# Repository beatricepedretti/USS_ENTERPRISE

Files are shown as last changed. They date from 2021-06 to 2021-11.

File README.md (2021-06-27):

# AY2021_II_Project_1-1

This repository contains the code and files for the Final Project 1 - Variant 1. Academic Year 2020/2021, II Semester

Our project consists in developing a system able to perform a three-dimensional scanning of an object using two servomotors (MG996R) and one ultrasonic sensor (HCSR04). Our sonar must be opportunely moved to detect the distance surfaces in the field of view of the USS.

<h2>Software requirements</h2>
In order to let our device perform the functionality previously described, some software requirements must be fulfilled. Since our codes are written in PSoC and python, the following IDEs and softwares must be downloaded:
<ul>
  <li>PSoC Creator</li>
  <li>Kivy</li>
  <li>Visual Studio Code</li>
  <li>MATLAB 2017b version with Computer Visio Toolbox</li>
  <li>Autodesk Fusion 360</li>
</ul>

<h2>Hardware requirements</h2>

In order to create our device different components have been used. 
<ul>
  <li>Two servomotors</li>
  <li>Connection elements in order to link the two servomotors and create a serial chain able to scan the proximal environment
  <li>An ultrasonic sensor, the HCSR04</li>
  <li>A cypress board</li>
  <li>An homemade wooden box that acts as a housing for the board and guarantees robustness and stability to the serial chain</li>
</ul>
All these components must be properly handled as follow.

<h3>Board settings</h3>

The board is placed inside the wooden box with custom sliding plexiglass cover, and it is powered by the computer. The connection between the board and the computer can be performed using any COM the user wants, it will be recognized by our code. 

<h3>Servomotors settings</h3>

The first servomotor must be connected to 2.6 PIN and it must have the crankshaft positioned vertically. The second servomotor must be connected at the 2.7 PIN and placed at the top of the first servomotor with the crankshaft positioned horizontally. Both of the servos need an external power supply in order to work properly.

<h3>Ultrasonic sensor settings</h3>

The HCSR04 must be linked to the crankshaft of the second servomotor through a special connection element in order to move solidly with this crankshaft. It works thanks to two connections, the Echo, the Trigger, that must be connected respectively to the 2.5 and 2.4 PINs. The cables are shielded with copper wires to prevent interference from the servo motor wiring and help reduce electronic noise.

<h3>Complete device arrangement</h3>

This repository contains the 'CAD' folder with the solidworks file of our configuration. It is possible to recreate the device following the image, as long as the user has all the components listed before. 

<h2>Calibration procedure and angle-coordinates conversion</h2>

It is possible to see and understand the conversion from angles to three-dimensional coordinates in the image below. In the following chapter the computation, that allows the representation of the object put in front of our device, will be described.

<h3>X-Y-Z system</h3>

The Z-axis is the extension of the crankshaft of the first servomotor and it remains integral with it. This servomotor is placed in the exact middle of the X-axis so that the bottom of its crankshaft consists in the origin of the reference system. Y-axis is aligned with the direction of the long side of the first servo motor. REMEMBER: the second servomotor rotates jointly and solidally with the crankshaft of the first servomotor.

<h3>Angles description</h3>

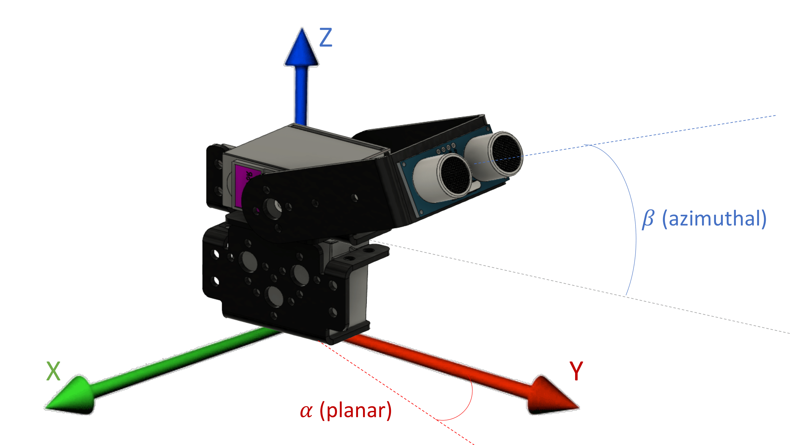
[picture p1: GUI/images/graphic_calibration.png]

 
The rotation of the crankshaft 1 allows to sweep the XY plane, its motion is described by the alpha angle. <i>Alpha is the angle between the Y-axis and the plane perpendicular to XY, containing the point detected and aligned with the direction of the arm to which the sonar is linked.</i><br>
The rotation of the crankshaft 2 allows to sweep the plane perpendicular to XY and aligned with the direction of the long side of the second servomotor and its motion is described by the beta angle. <i>Beta is the angle between the straight line determined by the arm to which the sonar is attached and the plane on which the crankshaft of the second servo motor lies.</i><br>
Functions getPosition() and setPosition(X°) allow to, respectively, return and set the angle (degrees) of one servo motor.  

First servomotor: 
<ul>
  <li>0 angle: lies on the positive portion of the X-axis</li>
  <li>90 angle: lies on the positive portion of the Y-axis</li>
  <li>180 angle: lies on the negative portion of the X-axis</li>
</ul>
In order to scan the width of the object put in front of the device, the first servomotor will sweep a 100° angle, starting from 40° up to 140°.

Second servomotor:
<ul>
  <li>0 angle: due to structural reason it consists in a 60° angle between the Z-axis and the straight line which is the extension of the arm to which the sonar is linked.</li>
  <li>90 angle: 0 angle + 90° = 150° (almost)</li>
</ul>
In order to scan the height of the object put in front of the device, the second servomotor will sweep a 60° angle, starting from 60° up to 120°.<br><br>
According to the information reported:<br>

SERVO_MID_ANGLE=90<br>
ANGLE_ZERO=60<br>
<i>alpha = SERVO_MID_ANGLE-Servo_GetPosition1()</i><br>
<i>beta = Servo_GetPosition2()+ANGLE_ZERO-SERVO_MID_ANGLE</i><br>

<h3>Coordinates computation</h3>

Knowing that :
<ul>
  <li>D2 is the distance between the middle of the crankshaft of the second servomotor and the Z-axis</li>
  <li>ARM_LENGTH is the length of the connection component that allows the rotation of the sonar solidally with the second crankshaft</li>
  <li>pos_servo1_rad is alpha in rad</li>
  <li>pos_servo2_rad is beta in rad</li>
  <li>pos_servo2_z_rad is beta+ANGLE_ZERO° in rad</li>
  <li>Z1 is the height of the crankshaft of the second servomotor</li>
</ul>
the coordinates computed using those two angles are:<br>

<i>X=(D2+(ARM_LENGTH+distance_real)*cos(pos_servo2_rad))*sin(pos_servo1_rad);</i><br>
<i>Y=(D2+(ARM_LENGTH+distance_real)*cos(pos_servo2_rad))*cos(pos_servo1_rad);</i><br>
<i>Z=Z1-(ARM_LENGTH+distance_real)*cos(pos_servo2_z_rad);</i><br>

<h2>Configuration through GUI</h2>
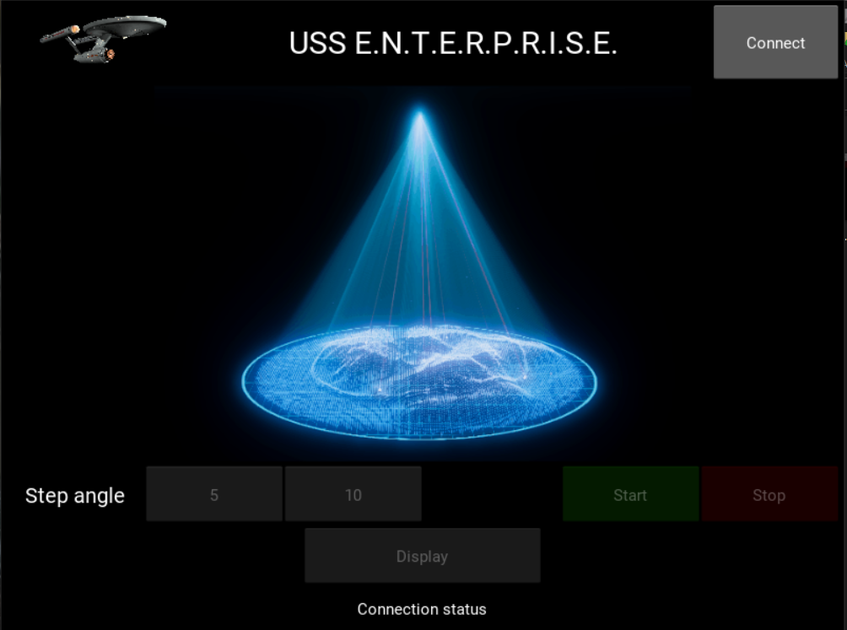
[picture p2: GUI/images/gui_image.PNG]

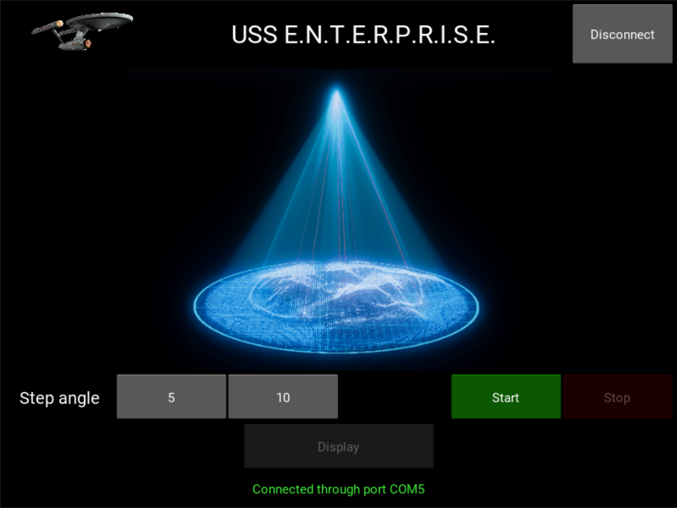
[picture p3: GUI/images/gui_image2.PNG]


Our GUI consists in six buttons: 
<ul>
  <li>Connect</li>
  <li>Start</li>
  <li>Stop</li>
  <li>Step angle, with two possibilities</li>
  <li>Display</li>
</ul>
and in a space filled with a GIF during the acquisition process.

<h3>UART communication settings</h3>

The user has the chance to connect automatically the GUI with the device through UART communication by pushing the button 'Connect'. If a board programmed with our code is connected to the computer, it will send back the string 'Device succesfully connected$' and our computer will understand which is the right COM to use. <br> After the 'Connect' button has been pressed, it changes name to 'Disconnect'. If 'Disconnect' button is pressed all the peripherals are turned off.<br>It will be possible to see at the bottom of the GUI the connection status  

<h3>Step angle settings</h3>

The user can also configure the <em>Step angle</em> of the servomotors through our GUI. This operation allows the user to obtain a more defined image by increasing the steps of the servomotors and so the number of points that describe the surface.

<h3>Start and Stop commands</h3>

The user has to press the 'Start' button in order to start the three-dimensional scanning and the 'Stop' button can be pressed anytime the user wants. After the 'Stop' button has been pressed our device will come back at the 'zero configuration', ready to begin a new scanning process.

<h3>Stop functionality</h3>

If our device will not find any point during an entire sweep of the XY plane it will automatically reset to the zero configuration (no object has been found or object scanning ended).

<h3>Display command</h3>

This button will be disabled until the end of the acquisition. Once the acquisition is done the 'display' button will be activated. The user will be able then to push it and display the reconstructed image.<br> The reconstructed image consists in a point cloud that appears inside a pop-up.<br> The user has also the chance to change the perspective of the object using the mouse. <i><U>Additional functionality: by pushing the 'p' key a screenshot will be performed and saved in the repository</U></i>. 

<h2>Operating instructions</h2>

<h3>Distance suggestion</h3>

Due to its dimensions and due to specific hardware limits, this device is able to understand the shape and concavity of an object with small dimensions. The object, moreover, MUST be placed at a distance between approximately 7 and 50 cm in order to have a higher quality reconstruction, otherwise the device will not be able to detect properly the object's surface. <b>Recommended</b> distance is in the 10 - 25 cm range. <br>

<h3>Positioning suggestion</h3>

Sweep on the XY plane is performed with a 100° angle; more specifically, the first servo motor goes from 40° to 140°, so alpha will go from 50° to -50°. The object should be put at the centre of this range in order to let the device scan the entire shape.

<h3>Limits considerations</h3>

Please be advised that, by nature, the sonar will return correct distances only for points on planes parallel or almost parallel to it. Our device, instead, works by rotating around two pins, and it does not use sliding tracks. For this reason, distances detected at the limits of our 100° range could be affected by bias. In order to manage this conditions we decided to narrow the sweeping range to 100° and to
suggest the user to scan small dimension objects. By doing this we let the sonar to work in its optimal conditions. 

<h2>Repository organization</h2>
Inside this repository you will find the following files and folders: 
<ul>
  <li>FinalProject_1-1.cydsn: folder containing PSOC Creator files</li>
  <li>GUI:</li>
  <ul>
  	<li><i>GUI.kv</i>: graphic implementation of GUI</li>
  	<li><i>Project_1_1.py</i>: python file containing GUI commands and image reconstruction</li>
  	<li><i>interpolation_plane.m</i>: MATLAB script with one section to reconstruct point cloud representation with axes (needs Computer Vision Toolbox) and another section that interpolates a plane in the point cloud representation (usefull to understand the quality of the reconstruction for <i>planar</i> objects)</li>
  	<li><i>requirements.txt</i>: required python libraries and dependencies</li>
  </ul>
  <li>coordinates: folder that contains acquisition results of relevant objects such as planes and bottles</li>
</ul>

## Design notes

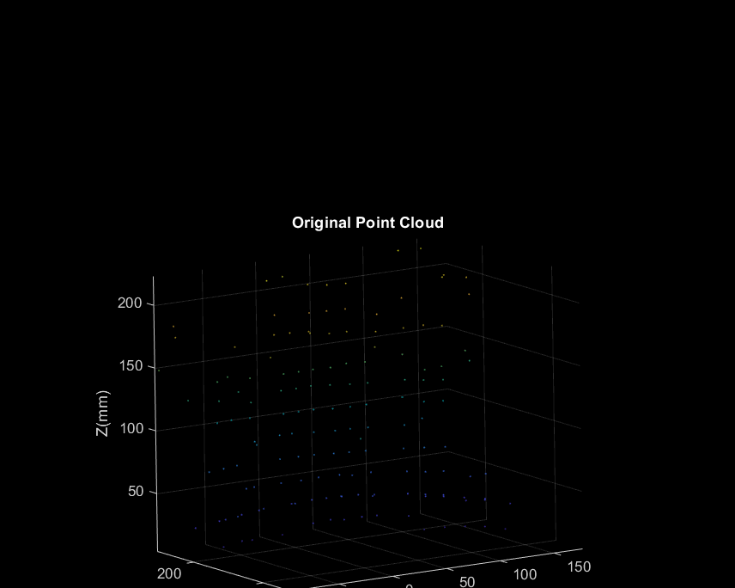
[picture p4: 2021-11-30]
Animation.gif

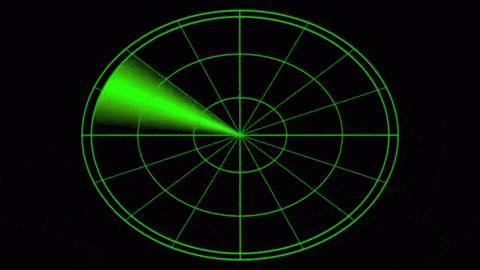
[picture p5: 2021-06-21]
GUI/images/vqr9LA.gif

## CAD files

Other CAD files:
cad/project1-1 v1.f3z

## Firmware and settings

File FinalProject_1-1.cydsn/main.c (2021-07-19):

/* =========================================================
 *
 * U.S.S. E.N.T.E.R.P.R.I.S.E.
 * Ultrasound Sensor for ENvironmenT Recording and
 * Point-cloud Reconstruction Integrated Scanning Equipment
 * 
 * Electronic Technologies and Biosensors Laboratory
 * Final Project
 * 
 * Di Liddo, Goshen, Pedretti
 *
 * =========================================================
*/

#include "project_utils.h"

int main(void)
{ 
    uint16_t angle;
    uint8_t temp_position;
    //upon turning on, state is IDLE and all peripherals are turned on
    state = IDLE;
    CyGlobalIntEnable; /* Enable global interrupts. */
    // Init components 
    start_components();
    ISR_HCSR04_Enable();
    //set both servo motors to starting position if they are not already 
    if (Servo_GetPosition1()!=SCAN_LIMIT_L || Servo_GetPosition2 ()!= SERVO_LIMIT_L)
        reset_servos();
    //every time I turn on the device, reset variables
    reset_variables();
    //reset sweep step to 5 degrees in case the step is not selected by the user
    step_sweep = 5;
    
        
    for(;;)
    {
        switch (state)
        {   
            //IDLE state: wait for user to press "START" in GUI
            //while in idle state, the user can select the step for the sweep between two choices
            case IDLE:
                //disable ISR: we on't need distance computation at the moment
                //ISR_HCSR04_Disable();
                if (Servo_GetPosition1()!=SCAN_LIMIT_L || Servo_GetPosition2 ()!= SERVO_LIMIT_L)
                    reset_servos();
                //this flag is set in the isr: if I just pushed connect in the GUI, I have to start the components (I come from the DISCONNECTED state)
                
                if (flag_connected == 1)
                {
                    start_components();
                    flag_connected  = 0;
                    sprintf (message1, "Device succesfully connected$");
                    UART_PutString(message1);
                }
                //if user selects '5' in GUI, UART sends over 'f' character and step_sweep is set to 5
                if (received == 'f')
                {
                    step_sweep = 5;
                }
                //same happens if the user selects '10'
                else if (received == 't')
                    step_sweep = 10;
                
                //reset variables but NOT step_sweep
                reset_variables();
                break;
            
            //SCAN state: the chain performs the sweep motion while the ISR activates and reads values from the  sensor
            case SCAN:
                //I don't use flags for enabling the ISR because after this line, the program gets stuck in the following for cycle
                //until the acquisition is stopped via GUI or scan is completed
                //so ISR is enabled only once
                //ISR_HCSR04_Enable();
                //FIRST SWEEP: the servo starts at 40 degrees, which is the first start position, and goes on until 140 degrees
                //the increment is the step selected in the GUI
                //this for cycle goes on until the state is SCAN (second condition)
                //the increment is multiplied by the direction of the sweep, anticlockwise (LEFT, value 1) or clockwise (RIGHT, -1)
                for (angle = start_position; angle != end_position/step_sweep && state == SCAN; angle+=(step_sweep*direction))
                {
                    Servo_SetPosition1(angle);
                    //wait for servo to be in position
                    CyDelay(SWEEP_DELAY);         
                    //read the value of the angle
                    //the servos' resolution is a mechanical limitation, so we check if the angle we set (known position) and the position we read are the same
                    //because different positions could lead to wrong calculations
                    //we still give a confidence value, which is a range of (ANGLE_TOLERANCE) degrees above and below the position we set
                    //so if the servos give a wrong position that is within this range, the point is still computed as the difference is low
                    if (Servo_GetPosition1()<(angle+ANGLE_TOLERANCE) && Servo_GetPosition1()>(angle-ANGLE_TOLERANCE))
                        //find position is a function in sonar.c as it involves the USS
                        find_position();   
                    //we enter this if below when we complete a "row", so when the chain does a sweep in one direction
                    if ((direction==LEFT && angle==end_position) || (direction == RIGHT && angle == (end_position+step_sweep)) )
                    {
                        //the following is a flag that is checked in sonar.c
                        //it is reset each row, and if becomes 1 if at least one point in that row is computed
                        //if this flag is still 0 after I completed a row, I assume that there isn't an object, 
                        //or that the object scanning is complete, or that the object has been removed
                        //so if I don't find any points within the range in an entire row, scanning is considered complete
                        if (flag_print == 0)
                            state = DISPLAY;
                        //this is a function in project_utils.c that moves the chain up by 5 degrees
                        next_row();
                        flag_print = 0;
                        //swap start and end positions for the sweep
                        temp_position = end_position;
                        end_position = start_position;
                        start_position = temp_position;
                        //swap directions
                        direction = direction == LEFT ? RIGHT : LEFT;
                    }        
                }
                break;
            
            //state DISPLAY is mainly performed in the GUI
            //here we simply consider the scanning as ended so we reset everything and go back to IDLE state immediately
            //we go back to IDLE in case that the user wants to start another scan
            case DISPLAY:
                if (Servo_GetPosition1()!=SCAN_LIMIT_L || Servo_GetPosition2 ()!= SERVO_LIMIT_L)
                    reset_servos();
                reset_variables();
                //redet step sweep
                step_sweep = 5;
                sprintf (message1, "Done scanning\r\n");
                UART_PutString(message1);
                state = IDLE;
                break;
            
            //state DISCONNECTED: when "Disconnect" button is pressed in the GUI, turn off components (except for UART)
            case DISCONNECTED:
                //i use the flag so that it turns off peripherals only once
                if (flag_disconnected == 1)
                {
                    Timer_HCSR04_Stop();
                    PWM_Trigger_Stop();
                    Timer_TRIGGER_Stop();
                    PWM_Servo1_Stop();
                    PWM_Servo2_Stop();
                    //ISR_HCSR04_Disable();
                    flag_disconnected = 0;
                    step_sweep = 5;
                }
                break;
        }      
    }
} 


/* [] END OF FILE */

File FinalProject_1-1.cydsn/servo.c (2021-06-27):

/* =========================================================
 *
 * U.S.S. E.N.T.E.R.P.R.I.S.E.
 * Ultrasound Sensor for ENvironmenT Recording and
 * Point-cloud Reconstruction Integrated Scanning Equipment
 * 
 * Electronic Technologies and Biosensors Laboratory
 * Final Project
 * 
 * Di Liddo, Goshen, Pedretti
 *
 * =========================================================
*/

#include "project_utils.h"

//This function sets both servo motors to start position
void reset_servos (void)
{
    Servo_SetPosition2(SERVO_LIMIT_L);
    CyDelay(SWEEP_DELAY);
    Servo_SetPosition1(SCAN_LIMIT_L);
    CyDelay(SWEEP_DELAY);    
}


/**
 *  \brief          Map value in new interval.
 *  \param[in]      x: the value to be remapped.
 *  \param[in]      in_min: minimum value for input interval.
 *  \param[in]      in_max: maximum value for input interval.
 *  \param[out]     out_min: minimum value for output interval.
 *  \param[out]     out_max: maximum value for output interval.
 *  \return         the remapped value.
 */
uint16_t Servo_Map(uint16_t x, uint16_t in_min, uint16_t in_max, uint16_t out_min, uint16_t out_max) {
    
    return (x - in_min) * (out_max - out_min) / (in_max - in_min) + out_min;
    
}

/**
 *  \brief          Set the servo to a new angle.
 *  \param[in]      deg: the degree angle to be set.
 *  \return         PWM compare value correspondent to the angle.
 */
uint16_t Servo_SetPosition1(uint16_t deg) {
 
    // Get the compare value for the desired position
    float tmp = Servo_Map(deg, SERVO_LIMIT_L, SERVO_LIMIT_H, SERVO_PWM_LIMIT_L, SERVO_PWM_LIMIT_H);
    
    // Update the PWM compare value
    uint16_t compareValue = round(tmp);
    PWM_Servo1_WriteCompare(compareValue);
    
    return compareValue;
    
}

uint16_t Servo_SetPosition2(uint16_t deg) {
 
    // Get the compare value for the desired position
    float tmp = Servo_Map(deg, SERVO_LIMIT_L, SERVO_LIMIT_H, SERVO_PWM_LIMIT_L, SERVO_PWM_LIMIT_H);
    
    // Update the PWM compare value
    uint16_t compareValue = round(tmp);
    PWM_Servo2_WriteCompare(compareValue);
    
    return compareValue;
    
}

/**
 *  \brief          Get the current position of the servo.
 *  \return         The servo motor angle.
 */
uint16_t Servo_GetPosition1(void) {
 
    // Get the actual compare value
    uint16_t comparePWM = PWM_Servo1_ReadCompare();
    
    // Map the value to degrees
    return Servo_Map(comparePWM, SERVO_PWM_LIMIT_L, SERVO_PWM_LIMIT_H, SERVO_LIMIT_L, SERVO_LIMIT_H);
    
}

uint16_t Servo_GetPosition2(void) {

    // Get the actual compare value
    uint16_t comparePWM = PWM_Servo2_ReadCompare();
    
    // Map the value to degrees
    return Servo_Map(comparePWM, SERVO_PWM_LIMIT_L, SERVO_PWM_LIMIT_H, SERVO_LIMIT_L, SERVO_LIMIT_H);
    
}

/* [] END OF FILE */

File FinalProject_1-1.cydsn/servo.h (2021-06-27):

/* =========================================================
 *
 * U.S.S. E.N.T.E.R.P.R.I.S.E.
 * Ultrasound Sensor for ENvironmenT Recording and
 * Point-cloud Reconstruction Integrated Scanning Equipment
 * 
 * Electronic Technologies and Biosensors Laboratory
 * Final Project
 * 
 * Di Liddo, Goshen, Pedretti
 *
 * =========================================================
*/

#ifndef __SERVO_H
    #define __SERVO_H
    
    #ifdef __cpluscplus
        extern "C" {
    #endif
    
    #include "project_utils.h"
    #include "PWM_Servo1.h"
    #include "PWM_Servo2.h"    
    
    /*************************************
     *          API Constants            *
     ************************************/

    //Lowest scanning limit 
    #define SCAN_LIMIT_L 40
    
    //Highest scanning limit
    #define SCAN_LIMIT_H 140
    
    //Lowest servo angle
    #define SERVO_LIMIT_L   0

    //Highest servo angle
    #define SERVO_LIMIT_H   180
    
    //Offset servo2
    #define ANGLE_ZERO 60
    
    //Middle servo angle
    #define SERVO_MID_ANGLE 90
    
    //PWM Compare value for \ref SERVO_LIMIT_L angle
    #define SERVO_PWM_LIMIT_L   1547

    //PWM Compare value for \ref SERVO_LIMIT_H angle
    #define SERVO_PWM_LIMIT_H   1399
    
    void reset_servos (void);
    
    uint16_t Servo_Map(uint16_t x, uint16_t in_min, uint16_t in_max, uint16_t out_min, uint16_t out_max);
    uint16_t Servo_SetPosition1(uint16_t deg);
    
    uint16_t Servo_SetPosition2(uint16_t deg);
    uint16_t Servo_GetPosition1(void);
    uint16_t Servo_GetPosition2(void);
    
    void Servo_MotionProfileBlocking(uint16_t xi, uint16_t xf, uint8_t t);
    
    #ifdef __cpluscplus
        extern }
    #endif
#endif

/* [] END OF FILE */

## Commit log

2021-05-19 added servo2 functions
2021-05-26 checked working of two servos
2021-05-26 working servos
2021-05-26 working sonar
2021-05-26 fixed sonar problem
2021-05-26 Added functions and servo1 sweep
2021-05-30 Measured sensor size
2021-06-09 added UART functionalities
2021-06-09 fixed bug in gui functionality
    [main.c, project_utils.c, project_utils.h]
2021-06-12 added resetting position option
    [main.c]
2021-06-12 changed position for printing coordinates
2021-06-18 main with some issues
    [isr.c, main.c]
2021-06-20 working chain, and saving coordinates
2021-06-21 fixed cinematic chain movement
    [isr.c, main.c, project_utils.c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]
2021-06-22 added display button and image insertion
2021-06-22 fixing GUI and PSOC code
    [Project_1_1.py, main.c, project_utils.c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]
2021-06-22 fixed UART
2021-06-23 back to isr
    [poisson.obj, poisson.ply]
2021-06-23 working code, reconstructed plane
    [poisson.obj, poisson.ply]
2021-06-23 matlab script for interpolation of regression plane
    [poisson.obj, poisson.ply]
2021-06-24 matlab file, point cloud, coordinates acquisition
    [poisson.obj, poisson.ply]
2021-06-24 added comments to PSOC
    [poisson.obj, poisson.ply]
2021-06-26 fixed angle servomotor 2
2021-06-26 moved files
    [ballpoint.obj, ballpoint.ply, poisson.obj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]
2021-06-26 graphic calibration env added
2021-06-26 cad added for inventor and fusion environment
    [##Servo_MG_996R.ipt, ##Servo_MG_996R_1.ipt, 0603 Capacitor.ipt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]
2021-06-26 fixing check on distance
    [sonar.c]
2021-06-26 fixed bugs and gui
    [Project_1_1.py, isr.c, main.c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]
2021-06-26 graphic env added
    [##Servo_MG_996R.SLDPRT, Assembly1.stp, MG996 v1 v12.f3d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]
2021-06-27 graphic env x fusion360
    [##Servo_MG_996R.SLDPRT, ##Servo_MG_996R.ipt, ##Servo_MG_996R_1.ipt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]
2021-06-27 uart name
2021-07-19 power point presentation
